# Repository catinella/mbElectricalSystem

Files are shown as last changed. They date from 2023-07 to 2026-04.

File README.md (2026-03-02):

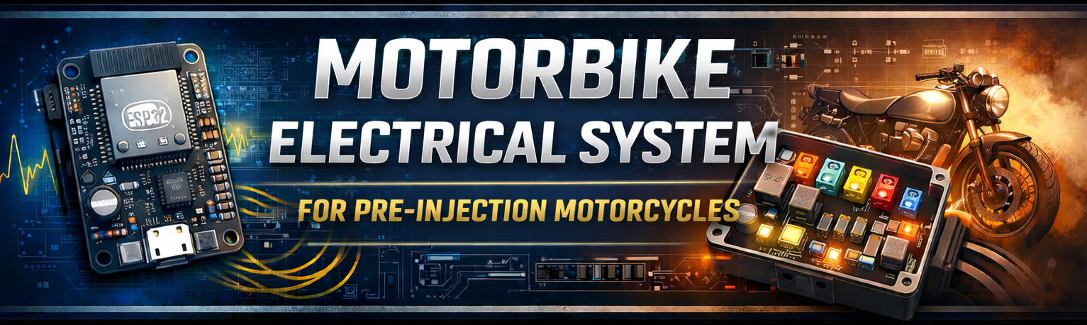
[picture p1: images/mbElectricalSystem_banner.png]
Project's banner

> Modular electrical control unit for pre-injection motorbikes  
> based on ESP32 and distributed power management

## 1.0 Files

| Files/Dirs | Description |
|---|---|
| firmware-esp32 | Firmware for the device's brain |
| images | Images used for README.md file |
| mechanical_parts | The CAD files for the device's box |
| PCB | All the PCB used by the device |

## 2.0 Description:
This project (MBES) aims to realize a generic motorbike electric system you can use on any old motorbike, or customized ones.

Pre-injection motorbikes typically leave the factory with a bulky and highly distributed wiring harness. All power and control
lines are routed through a single large cable bundle, creating what can be described as an “electrical snake”.

Opening this harness often feels like exposing the internal organs of that snake: a dense mass of wires embedded in adhesive
tape and protective compounds. Identifying a single faulty line inside this structure can quickly become a nightmare.

No more chaotic situations with this modern motorbike electrical system: the (bigger) power bales will run just from the device
to the user (light, horn, indicators....) and all commands' cables (light switch, start button, turn indicators switches...)
will be smaller because very small electric current will flow inside them.

### 2.1 Managed devices:
- High beam and down beam headlights
- Left and right turn flashing indicators
- Additional (high power) light
- Horn
- Neutral, left/right indicators, high/down light... LEDs
- STOP light
- Engine start button
- Motorbike (and engine) OFF switch
- Clutch switch
- Decompressor command management
- External cockpit power-connector
- Cockpit's leds

### 2.2 Provided features
- Checking for decompressor command
  The system does not allow the engine to run, before the decompressor command has been activated.
  If the veichle does not have a decompressor system, or if the level control switch is broken, then this feature can be
  disabled easily.

- Direction indicator blinking
  Common blinking for the yellow indicator. The system has been planed for 12V LED indicators (with resistors), but because
  for these ports 2A current can be supported, you can also use older lights

- Resistive authentication key
  In order to turn-on the motorbike, the driver must insert a valid resistor key. After the autentication the key
  can be also removed. It is very usefull for off-road using. 

- Parking mode
  To set the motorbike turned-off but with the normal-light-on and the indicators blinking, you have to put the
  motorbile stopped on its lateral stand, set the engine swith to off, and turn the normal-light on. In this mode the engine
  cannot be started. To restart the veichle you have to turn-off it with the proper switch
	
### 2.3 Security rules:
- Byke stand
  if the motorcycle stand is downn when the engine is connected to the wheels, the the engine will be stopped

- Decompressor command
  If the motorcycle is running and the driver will push the decompressor command, then the engine will be stopped

## 3.0 Info about this version:
This branch is based on ESP32 MCU. This chip is a powerful and very low-price device and it allowed me to reduce the PCB
size. At the moment, I am using the ESP32 devkit device because welder this chip is a bit difficult operation.
This branch solution provides just one PCB. It has further reduced the PCB size.

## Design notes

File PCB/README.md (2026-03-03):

Project's banner

## 1.0 Files

| Files/Directories | Description |
|---|---|
| Connectors.txt | Cables's connectors pin-out |
| create_fabric_files.sh | Script to create the fabric files |
| kicad_symbols | Non standard KiCAD symbols libraries |
| LICENSE.txt | The project's licence file (\*) |
| main.kicad_pcb | The PCB file |
| main.kicad_sch | The main electronic circuit schema |
| mbes_front_outputs.kicad_sch | Power stage circuit |
| mbes_pcbA_connectors.kicad_sch | PCB's connectors electronic circuit  |
| starter_key_plug | The schema of the resistive key |
| images | The images used by this file |

(*) This project is covered by the GPL-3. Please, read that file for further information

## 2.0 Description:
This folder contains all files you need to get and/or modify your own PCB.
To perform these actions you need to install [KiCAD](https://www.kicad.org) software (ver >= 9.0), a free software suite for
electronic design automation (EDA).

## 2.1 Internals:
For the **power stage** I have use the [TPCA8120](https://static.chipdip.ru/lib/624/DOC060624975.pdf) P-Channel MOS. Its
low Drain-source on-resistance (4mOhm) allows me to avoid to waste electric power with high current too. For eample
with a 60W (5A) light it wase just 20mW!! It can also support 10A current and it is very small.

To reduce the number of fuses, the direction indicator LEDs use a [MSMF050](https://www.bourns.com/docs/product-datasheets/mf-msmf.pdf)
PTC Resettable Fuse.

As in all motorbikes, in order to avoid the engine can be started when the motorbike is locked, the proper CDI pin must be
connected to the GND. To achiueve this result and to protect the circuit from unknown electric voltage from the CDI, I have 
used the relay [HK19-DC12V](https://grobotronics.com/images/datasheets/HK19F-12V.pdf) instead of a modern N-Channel MOS.

## 3.0 Devices building:
The following images shows you the PCB shape it should be at the end
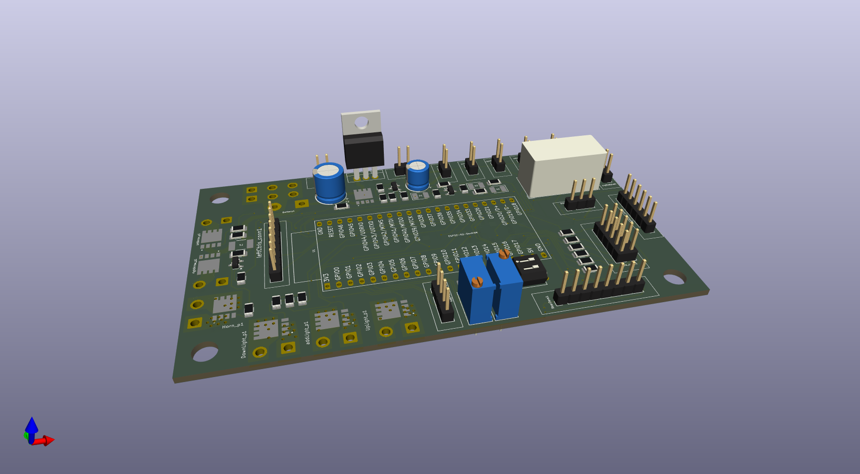
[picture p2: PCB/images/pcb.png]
PCB


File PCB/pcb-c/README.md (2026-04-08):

Project's banner

## 1.0 Files

| Files/Directories | Description |
|---|---|
| pcb-c.kicad_sch | Electric symbolic scheme |
| pcb-c.kicad_pcb | PCB |

(*) This project is covered by the GPL-3. Please, read that file for further information

## 2.0 Description:
This folder contains all files you need to build and/or modify the PCB placed in the rear side of the (DR350) motorbike.
This circuit is a small power stage for the rear light indicators, stop light, and position light. Because all lights
are available in LED format, the power stage is set to provide maximum 500mA (6W) per device.

## 2.1 Internals:
In order to fit this device in the DR350 rear size, I have tried to reduce the required space as much as possible. Also
for this reason, normal fuses have been replaced by [MSMF050](https://www.bourns.com/docs/product-datasheets/mf-msmf.pdf)
PTC Resettable Fuses.

All the power stage's outputs are equivalent but one is dedicated to the motorbike's starter relay. This relay type can
be a big one, often. So, a fly-back diode is very important. For this reason I have used a 
[M7 Rectifiers Diode](https://diotec.com/request/datasheet/m1.pdf).

## 3.0 Devices building:
The following images shows you the PCB shape it should be at the end
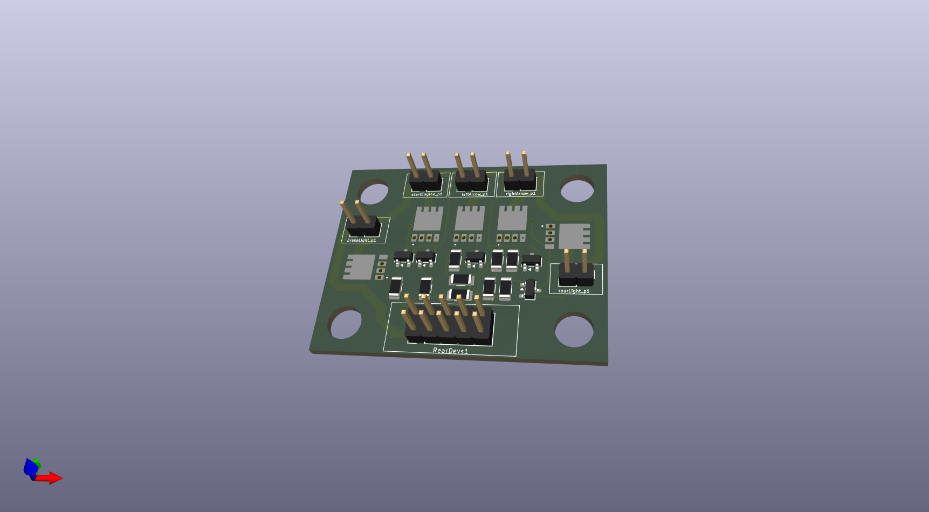
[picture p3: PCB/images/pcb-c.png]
PCB


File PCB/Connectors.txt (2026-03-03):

#-------------------------------------------------------------------------------------------------------------------------------
   __  __       _             _     _ _          _____ _           _        _           _   ____            _                 
  |  \/  | ___ | |_ ___  _ __| |__ (_) | _____  | ____| | ___  ___| |_ _ __(_) ___ __ _| | / ___| _   _ ___| |_ ___ _ __ ___  
  | |\/| |/ _ \| __/ _ \| '__| '_ \| | |/ / _ \ |  _| | |/ _ \/ __| __| '__| |/ __/ _` | | \___ \| | | / __| __/ _ \ '_ ` _ \ 
  | |  | | (_) | || (_) | |  | |_) | |   <  __/ | |___| |  __/ (__| |_| |  | | (_| (_| | |  ___) | |_| \__ \ ||  __/ | | | | |
  |_|  |_|\___/ \__\___/|_|  |_.__/|_|_|\_\___| |_____|_|\___|\___|\__|_|  |_|\___\__,_|_| |____/ \__, |___/\__\___|_| |_| |_|
                                                                                                  |___/                       
#-------------------------------------------------------------------------------------------------------------------------------

Motorbike controls connectors:
	In ordet to connect the handlebars electric (buttons/switches) conrols, I selected connectors based on 2.8mm faston.
	These connectors are widely used in automotive applications, but unfortunately I did not found a link to their
	documentation.

	Left connector pins-map:
	========================             +---+
	1) GND                         +-----+---+-----+
	2) Left turn indicator         | +-+  +-+  +-+ |
	3) Down-light                  | |4|  |5|  |6| |
	4) Dazzling light              | +-+  +-+  +-+ |
	5) Right turn indicator        | +-+  +-+  +-+ |
	6) Horn                        | |1|  |2|  |3| |
	7) Clutch switch               | +-+  +-+  +-+ |
	8) --- N.C. ---                +---------------+

	Right connector pins-map:
	=========================
	1) GND
	2) GND
	3) Brake control switch
	4) Engine START button
	5) Engine OFF
	6) Engine ON

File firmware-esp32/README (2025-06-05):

#----------------------------------------------------------------------------------------------------------------------------------
     __  __       _             _     _ _          _____ _           _        _           _   ____            _                 
    |  \/  | ___ | |_ ___  _ __| |__ (_) | _____  | ____| | ___  ___| |_ _ __(_) ___ __ _| | / ___| _   _ ___| |_ ___ _ __ ___  
    | |\/| |/ _ \| __/ _ \| '__| '_ \| | |/ / _ \ |  _| | |/ _ \/ __| __| '__| |/ __/ _` | | \___ \| | | / __| __/ _ \ '_ ` _ \ 
    | |  | | (_) | || (_) | |  | |_) | |   <  __/ | |___| |  __/ (__| |_| |  | | (_| (_| | |  ___) | |_| \__ \ ||  __/ | | | | |
    |_|  |_|\___/ \__\___/|_|  |_.__/|_|_|\_\___| |_____|_|\___|\___|\__|_|  |_|\___\__,_|_| |____/ \__, |___/\__\___|_| |_| |_|
                                                                                                    |___/                       
#----------------------------------------------------------------------------------------------------------------------------------
0. Files
	build            Folder for firmware building process
	CMakeLists.txt   The CMAKE config file to create the required Makefile
	main             Folder that contains the firmware source code
	sdkconfig        Project and device configuration

1. Description:
	This folder contains all needed files to build the project firmware

	Environment Configuration:
	==========================
	This firmware is based on Espressif's MCU ESP32-S2 and, in order to built it, you have to get and configure the esp-idf
	building environment. To complete the task, please, read the follow official documentation:
		https://docs.espressif.com/projects/esp-idf/en/v5.3.1/esp32/get-started/index.html
	
	Device Configuration:
	=====================
	In order to use the JTAG's pins as normal GPIOs you need to disable the JTAG support on your ESP32-S2 MCU with the
	following command:
		espefuse.py --port /dev/ttyUSB0 burn_efuse SOFT_DIS_JTAG

	Firmware Configuration:
	=======================
	From the 5.3 release esp-idf uses CMAKE as software building infrastructure (project.mk is no more available).
	For this rerason all configuration has been set in the CmakeLists.conf file. This file is parsed by the CmakeLists.txt
	file using the configUtils.cmake library. In order to get the options list, please, read the documentation lines in
	the CmakeLists.txt file's head.

	Building process:
	=================
	To build the firmware use the following idf standard command:
		idf.py build

	Debug console:
	==============
	In order to monitor the pin's status in real-time, you can use the debugConsole software in the <PROJECT HOME>/tool
	folder

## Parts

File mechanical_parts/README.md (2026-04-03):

Project's banner
> Modular electrical control unit for pre-injection motorbikes  
> based on ESP32 and distributed power management

## 1.0 Files

| Files/Dirs | Description |
|---|---|
| DR350_rally | Parts for Suzuki DR350 with rally components |

## 2.0 Description:
This folder contains all CAD and specifications documents dequired to build the Motorbike Electrical System's containers. The
CAD documents are 2D drawings and they show you the flat parts you will have to weller. Anyway, read the README.md file in the
proper sub-folder for further details.

In order to create all the CAD files I used [LibreCAD](https://librecad.org) 2D software. Anyway, because the files are DXF
standard ones, you can use your favourire CAD software.

Any CAD document is composed by (at least) three layers:
- 0        The effective drawing
- builder  Tracks used to build the drawing (you could set it to hidden layer)
- sizes    The measures you need to build the pasts hand made, or to check for their correct shapes

### 2.1 DR350 Rally
The motorbike I used as first model for this project, is a DR350 (1998) modified for off-road using. These changes include a couple
of 48mm Showa front shock absorber and a motorcycle fairing made by [Twalcom](https://www.twalcom.com/en). So the front side box can
be compatible with many similar motorbikes (KTM, Usqvarna...). Instead, the box located in the rear part is just for this motorbyke
model. Infact, the box fills the space originally used for the fuses-box, and the box's shape has been developed to be linked to that
framework in a solid way.

In order to mount this part on your DR350, you need to make 5mm diameter hole in the old metal fuses-box support.

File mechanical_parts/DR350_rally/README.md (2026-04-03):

Project's banner
> Modular electrical control unit for pre-injection motorbikes  
> based on ESP32 and distributed power management

## 1.0 Files

|  Files/Dirs  | Description |
|---|---|
| frontSide | Circuits container for the motorbike front side |
| rearSide | PCB container for the motorbike rear side |

## 2.0 Description:
In the original DR350's electric system, as every other with the same age, the electric current flows in (1mmq) big wires from
the commands to the services (lights, horn, relay...). But the commands are located on the hand-bar, in the front
side of the motorbike, while some services (turn-indicators, stop-light, emgine-start-relay...) is located in the rear one.
So, to reduce the number and the size of the wires that runs in the electric system, I have placed one power stage in the front
side and another in the rear side. Every one of them has its own metal box container.

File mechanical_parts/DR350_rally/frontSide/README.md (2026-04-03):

Project's banner
> Modular electrical control unit for pre-injection motorbikes  
> based on ESP32 and distributed power management

## 1.0 Files

|  Files/Dirs | Description |
|---|---|
| electricSystemBox.dxf | Electric system main-box |
| Koso_instrumentation_attachment.dxf  | Mechanical part used to mount the Koso's cocpit |
| electricSystemBox_squareBars.dxf | System used to close the box's lid |
| motorbikeFrame_attachment_system.dxf | Small plate used to link the box to the framework |

## 2.0 Description:

### 2.1 The Electric System (main) Box
This box can contain the PCB-A and PCB-B circuits. The CAD file shows you all the 2D parts you should create starting from a
3mm aluminium sheet. Mounting the parts to be welled in correct way, can be a difficult task, but you can use the square bars
support to get an advantage.

#### 2.1.1 How to close the box?
In order to close the box's lid, you have to lock the (**electricSystemBox_squareBars.dxf**) square bars inside the box with
3mm screws, then use 5mm screws to lock the lid of the box. For the 3mm screws mounting, I suggest youto use the
[Loctite Threadlocker Red](https://www.loctiteproducts.com/products/central-pdp.html/loctite-threadlocker-red/SAP_0201OHL029W5/variation/209741.html)
substance. You should not need to remove these screws, in the future.

**[IMPORTANT]** Because the bars are used as screw nut, it SHOULD NOT be made with aluminium, it SHOULD be produced using a
stainless steel metal.

#### 2.1.2 How to attach the box to the motorbyke framework?
In order to link the box to the motorbike's framework you should weld four 6MA bolts to the (2mm) plate described in the 
**motorbikeFrame_attachment_system.dxf** drawing. The plate should be placed inside the lid, on the box's bottom side. the
protruding bolts will be used to link the device to the franework in stable way.
The plate and the bolts should be built in stainless steel metal.

### 2.2 Koso's Cokpit
As motorbike cockpit I use a [KOSO's](https://www.koso.com.tw/en) product. To link this part to the upside of the box, you need
two copy of the mechanical single part described in the **Koso_instrumentation_attachment.dxf** CAD file. The file shows you two
sides of the object (from lateral and top point of view). It should be built with aluminium and it does not require to be welded.

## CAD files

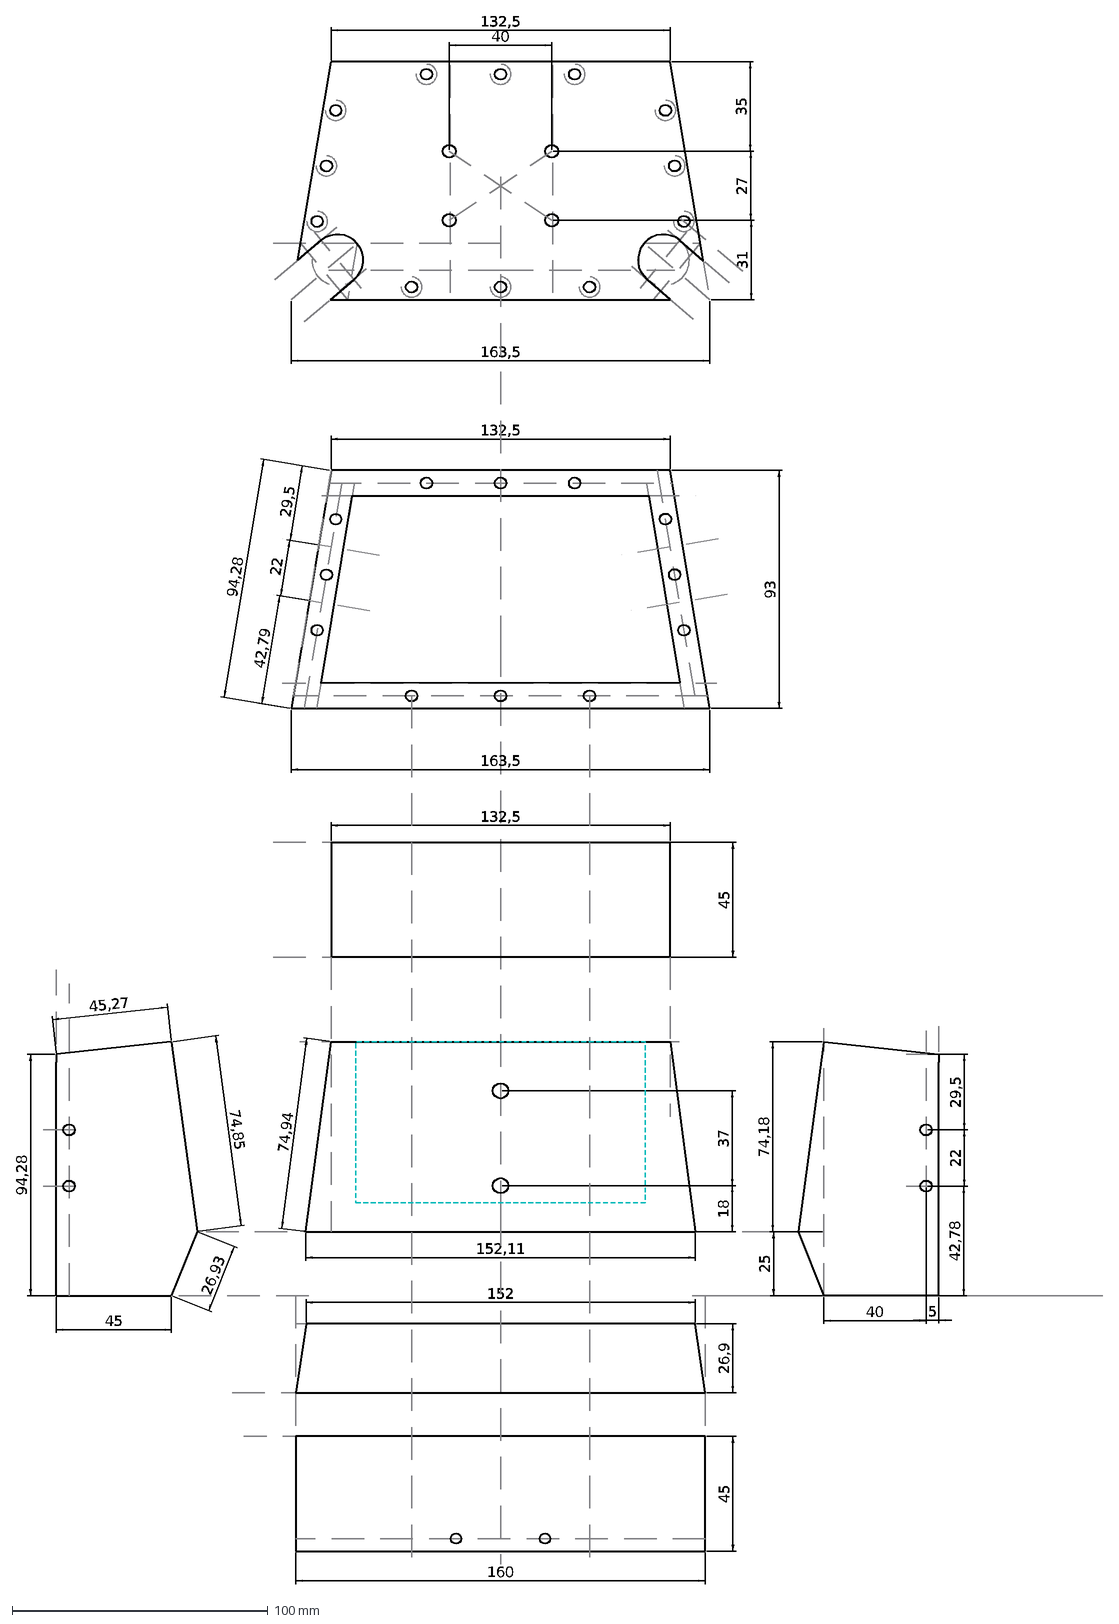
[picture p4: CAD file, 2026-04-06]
mechanical_parts/DR350_rally/frontSide/electricSystemBox.dxf
132,5
163,5
93
45
31
27
35
40
152,11
160
26,9
152
37
18
25
74,18
94,28
26,93
74,85
45,27
74,94
29,5
22
42,79
42,78
5

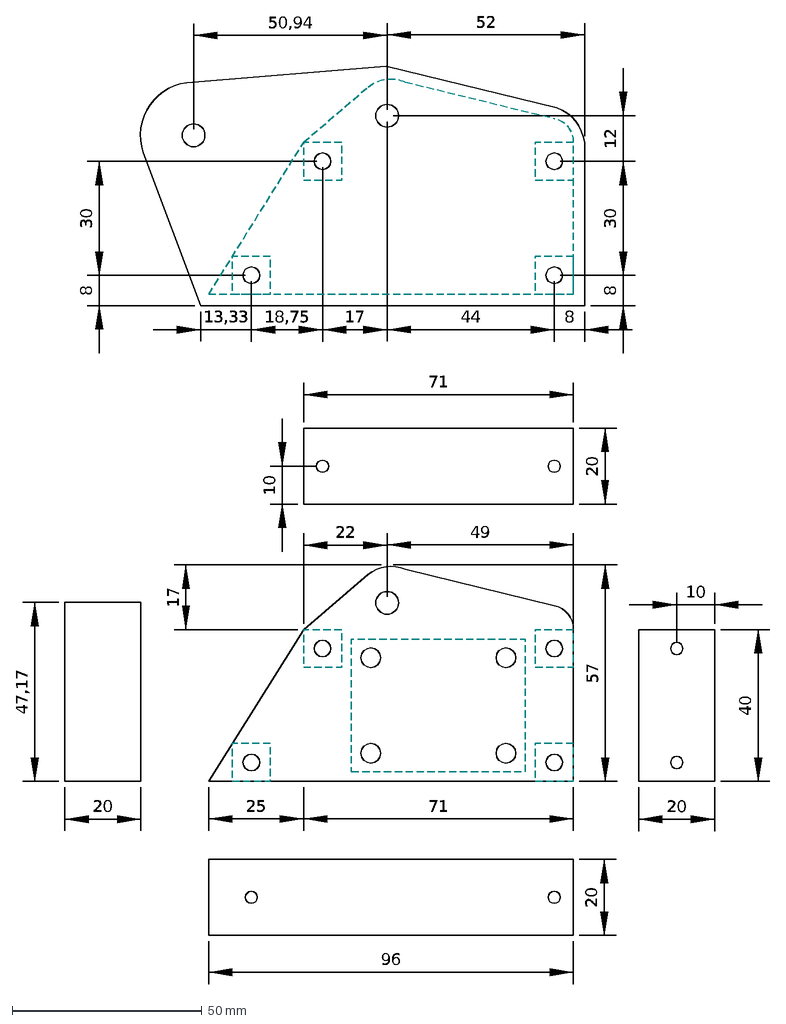
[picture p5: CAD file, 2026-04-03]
mechanical_parts/DR350_rally/rearSide/electricSystemBox.dxf
96
40
57
20
17
49
22
25
71
47,17
10
8
44
30
12
18,75
13,33
52
50,94

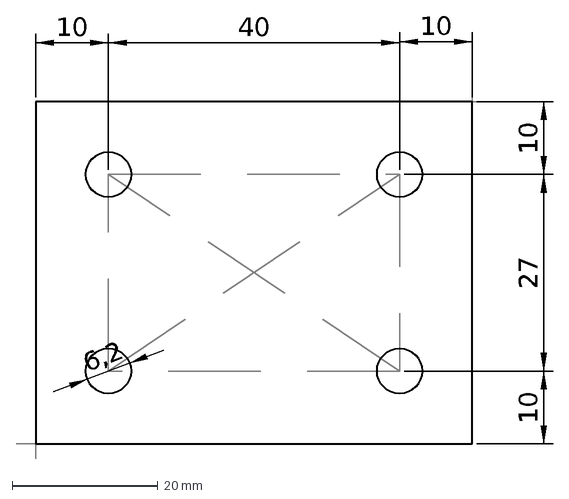
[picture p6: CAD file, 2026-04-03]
mechanical_parts/DR350_rally/frontSide/motorbikeFrame_attachment_system.dxf
10
27
40
6,2

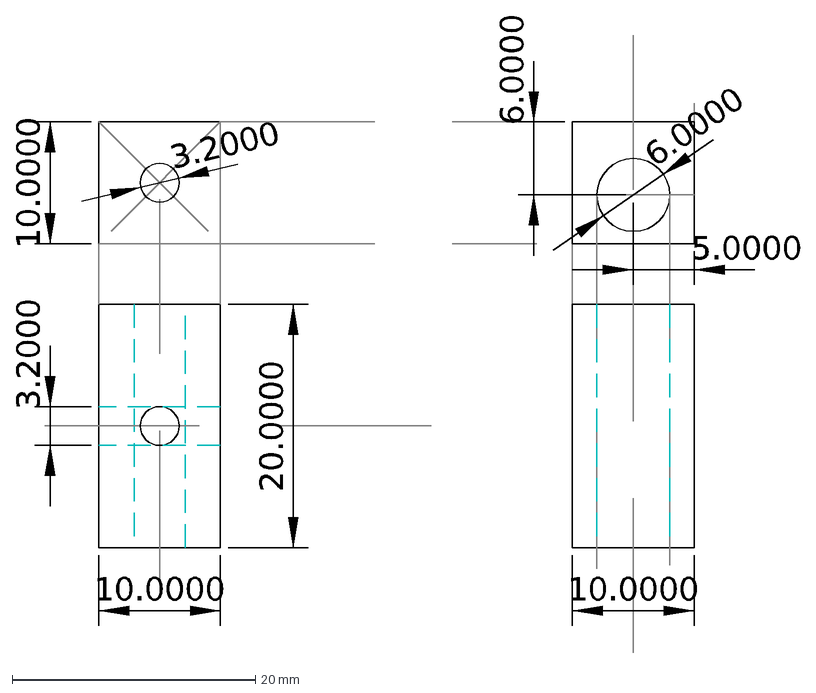
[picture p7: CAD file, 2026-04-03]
mechanical_parts/DR350_rally/rearSide/electricSystemBox_internalSupports.dxf
10.0000
3.2000
20.0000
6.0000
5.0000

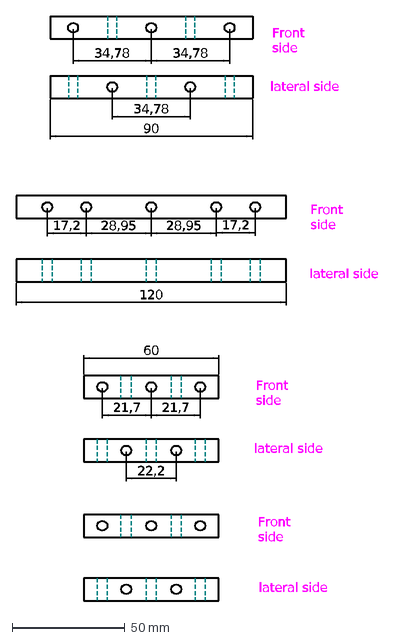
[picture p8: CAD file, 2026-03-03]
mechanical_parts/DR350_rally/frontSide/electricSystemBox_squareBars.dxf
34,78
28,95
17,2
120
60
90
21,7
Front side
lateral side
22,2

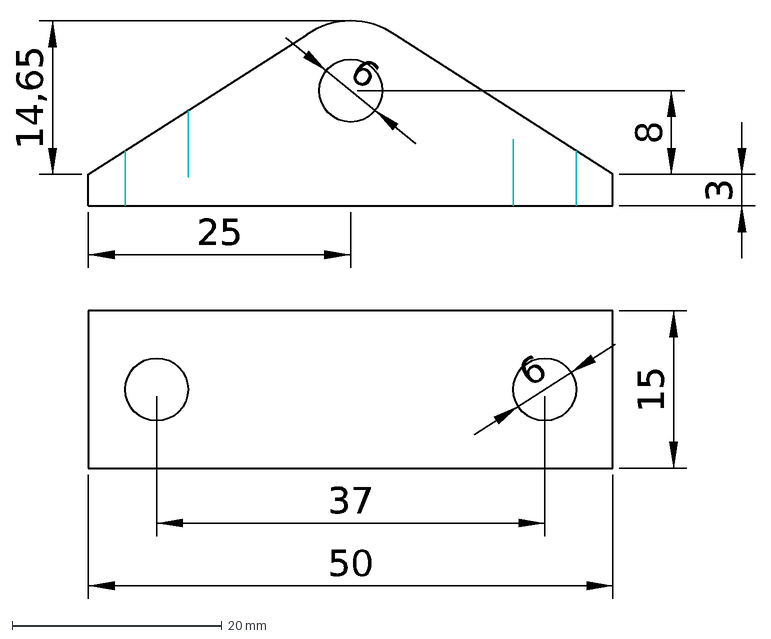
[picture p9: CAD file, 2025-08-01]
mechanical_parts/DR350_rally/frontSide/Koso_instrumentation_attachment.dxf
50
37
25
14,65
8
3
6
15

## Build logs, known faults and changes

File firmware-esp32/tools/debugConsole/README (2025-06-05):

#-----------------------------------------------------------------------------------------------------------------------------------
     __  __       _             _     _ _          _____ _           _        _           _   ____            _                 
    |  \/  | ___ | |_ ___  _ __| |__ (_) | _____  | ____| | ___  ___| |_ _ __(_) ___ __ _| | / ___| _   _ ___| |_ ___ _ __ ___  
    | |\/| |/ _ \| __/ _ \| '__| '_ \| | |/ / _ \ |  _| | |/ _ \/ __| __| '__| |/ __/ _` | | \___ \| | | / __| __/ _ \ '_ ` _ \ 
    | |  | | (_) | || (_) | |  | |_) | |   <  __/ | |___| |  __/ (__| |_| |  | | (_| (_| | |  ___) | |_| \__ \ ||  __/ | | | | |
    |_|  |_|\___/ \__\___/|_|  |_.__/|_|_|\_\___| |_____|_|\___|\___|\__|_|  |_|\___\__,_|_| |____/ \__, |___/\__\___|_| |_| |_|
                                                                                                    |___/                       
#-----------------------------------------------------------------------------------------------------------------------------------
0. Files
	debugConsole.c         C library
	debugConsole.h         Header file
	debugConsole.pl        DebugConsole executable file
	debugConsole_test.pl

1. Description:
	The code belongs to this folder allows you to get a serial debug console where the PINs status will be displayed with the
	log-messages, in ordered and clean way

2. Dependences:
	The process also need the "stty" system-tool to configure the serial port. But this tool should be already installed by
	default

3. Testing procedure
	Because this console receives data from serial port, to test it you need a virtual serial port. In order to get it, you
	can use the following command:
		socat -d -d pty,raw,echo=0 pty,raw,echo=0

	This command will generate a serial ports couple in /dev/pts folder. The two ports are linked like the head and the tail
	of a queue, it means when you send data to a port you can read the data from the other one.

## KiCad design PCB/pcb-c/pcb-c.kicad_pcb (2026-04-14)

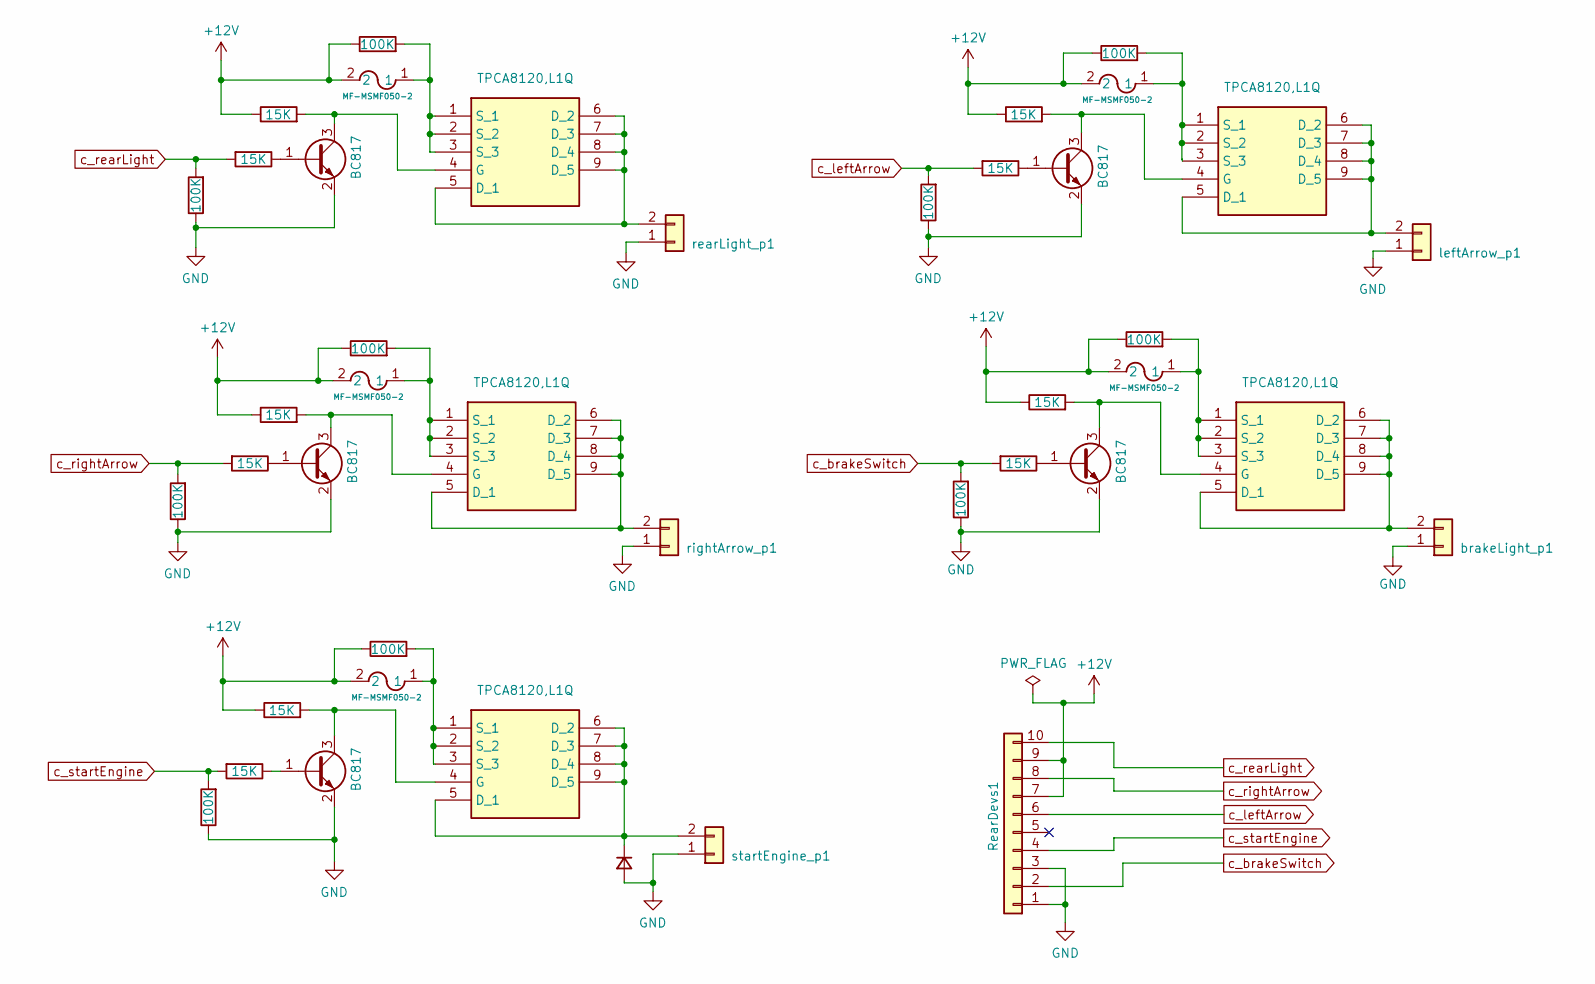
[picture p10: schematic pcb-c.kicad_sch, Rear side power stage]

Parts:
D1: M7; D_2114_3652Metric_Pad1.85x3.75mm_HandSolder
F1, F2, F3, F4, F5: MF-MSMF050-2; FUSE_F050-2
Q1, Q3, Q4, Q6, Q8: BC817; SOT-23
Q2, Q5, Q7, Q9, Q13: TPCA8120,L1Q; TPH4R003NLL1Q; Manufacturer_Part_Number TPCA8120,L1Q; Mouser Part Number 757-TPCA8120L1Q
R1, R3, R6, R8, R11, R12, R15, R16, R19, R21: 100K; R_1206_3216Metric
R2, R4, R5, R7, R9, R10, R13, R14, R17, R18: 15K; R_1206_3216Metric
RearDevs1: Conn_01x10; PinHeader_2x05_P2.54mm_Vertical
brakeLight_p1: Conn_01x02; PinHeader_1x02_P2.54mm_Vertical
leftArrow_p1: Conn_01x02; PinHeader_1x02_P2.54mm_Vertical
rearLight_p1: Conn_01x02; PinHeader_1x02_P2.54mm_Vertical
rightArrow_p1: Conn_01x02; PinHeader_1x02_P2.54mm_Vertical
startEngine_p1: Conn_01x02; PinHeader_1x02_P2.54mm_Vertical

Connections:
+12V: F1.2, F2.2, F3.2, F4.2, F5.2, R2.1, R3.1, R5.1, R6.1, R10.1, R11.1, R14.1, R15.1, R18.1, R19.1, RearDevs1.7, RearDevs1.9
GND: D1.2 (A), Q1.2 (E), Q3.2 (E), Q4.2 (E), Q6.2 (E), Q8.2 (E), R1.1, R8.1, R12.1, R16.1, R21.1, RearDevs1.1, RearDevs1.3, brakeLight_p1.1, leftArrow_p1.1, rearLight_p1.1, rightArrow_p1.1, startEngine_p1.1
unnamed: D1.1 (K), Q5.5 (D_1), Q5.6 (D_2), Q5.7 (D_3), Q5.8 (D_4), Q5.9 (D_5), startEngine_p1.2
unnamed: Q1.1 (B), R4.1
unnamed: Q1.3 (C), Q2.4 (G), R5.2
unnamed: Q2.5 (D_1), Q2.6 (D_2), Q2.7 (D_3), Q2.8 (D_4), Q2.9 (D_5), brakeLight_p1.2
unnamed: F2.1, Q2.1 (S_1), Q2.2 (S_2), Q2.3 (S_3), R6.2
unnamed: Q3.1 (B), R7.1
unnamed: Q4.1 (B), R9.1
unnamed: Q4.3 (C), Q5.4 (G), R10.2
unnamed: F5.1, Q5.1 (S_1), Q5.2 (S_2), Q5.3 (S_3), R3.2
unnamed: Q6.1 (B), R13.1
unnamed: Q6.3 (C), Q7.4 (G), R14.2
unnamed: Q7.5 (D_1), Q7.6 (D_2), Q7.7 (D_3), Q7.8 (D_4), Q7.9 (D_5), leftArrow_p1.2
unnamed: F4.1, Q7.1 (S_1), Q7.2 (S_2), Q7.3 (S_3), R15.2
unnamed: Q8.1 (B), R17.1
unnamed: Q8.3 (C), Q9.4 (G), R18.2
unnamed: Q9.5 (D_1), Q9.6 (D_2), Q9.7 (D_3), Q9.8 (D_4), Q9.9 (D_5), rightArrow_p1.2
unnamed: F1.1, Q9.1 (S_1), Q9.2 (S_2), Q9.3 (S_3), R11.2
unnamed: Q13.5 (D_1), Q13.6 (D_2), Q13.7 (D_3), Q13.8 (D_4), Q13.9 (D_5), rearLight_p1.2
unnamed: Q3.3 (C), Q13.4 (G), R2.2
unnamed: F3.1, Q13.1 (S_1), Q13.2 (S_2), Q13.3 (S_3), R19.2
c_brakeSwitch: R1.2, R4.2, RearDevs1.2
c_leftArrow: R12.2, R13.2, RearDevs1.6
c_rearLight: R7.2, R21.2, RearDevs1.10
c_rightArrow: R16.2, R17.2, RearDevs1.8
c_startEngine: R8.2, R9.2, RearDevs1.4

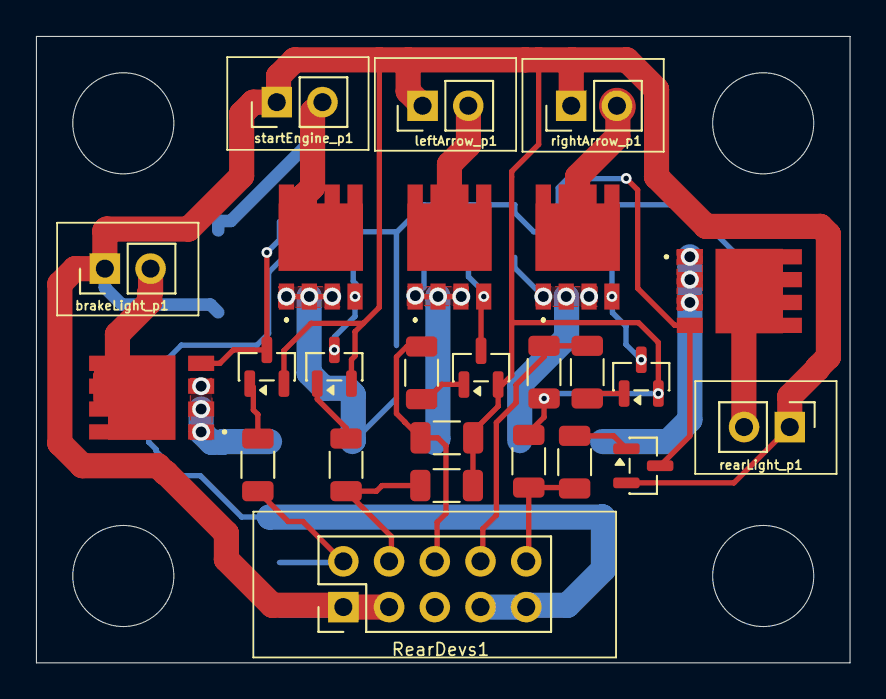
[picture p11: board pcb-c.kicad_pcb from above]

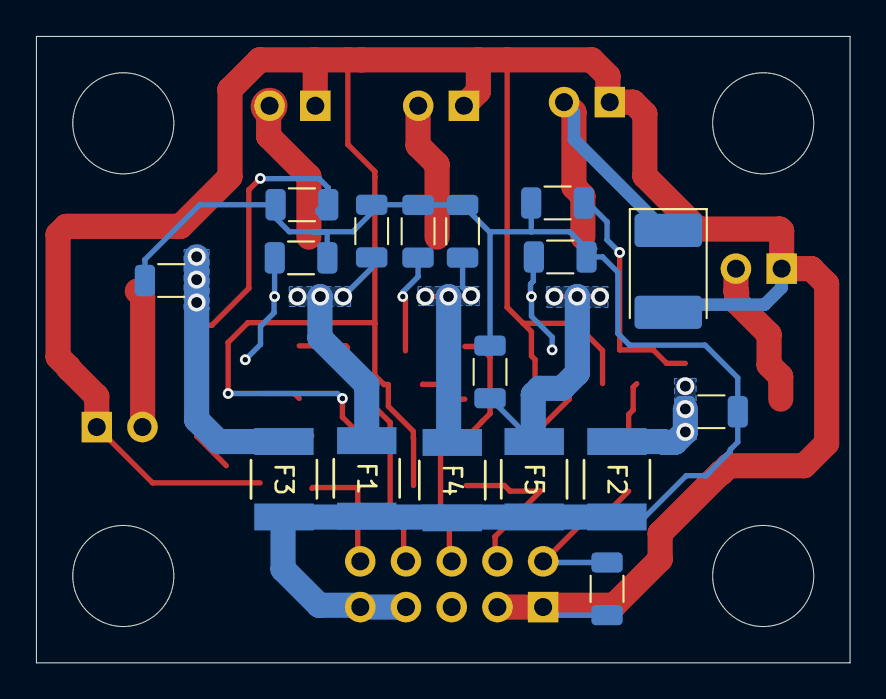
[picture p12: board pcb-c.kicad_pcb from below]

Board: 2 copper layers, 45.2 x 34.8 mm, 42 parts (17 on the bottom side), 27 nets.

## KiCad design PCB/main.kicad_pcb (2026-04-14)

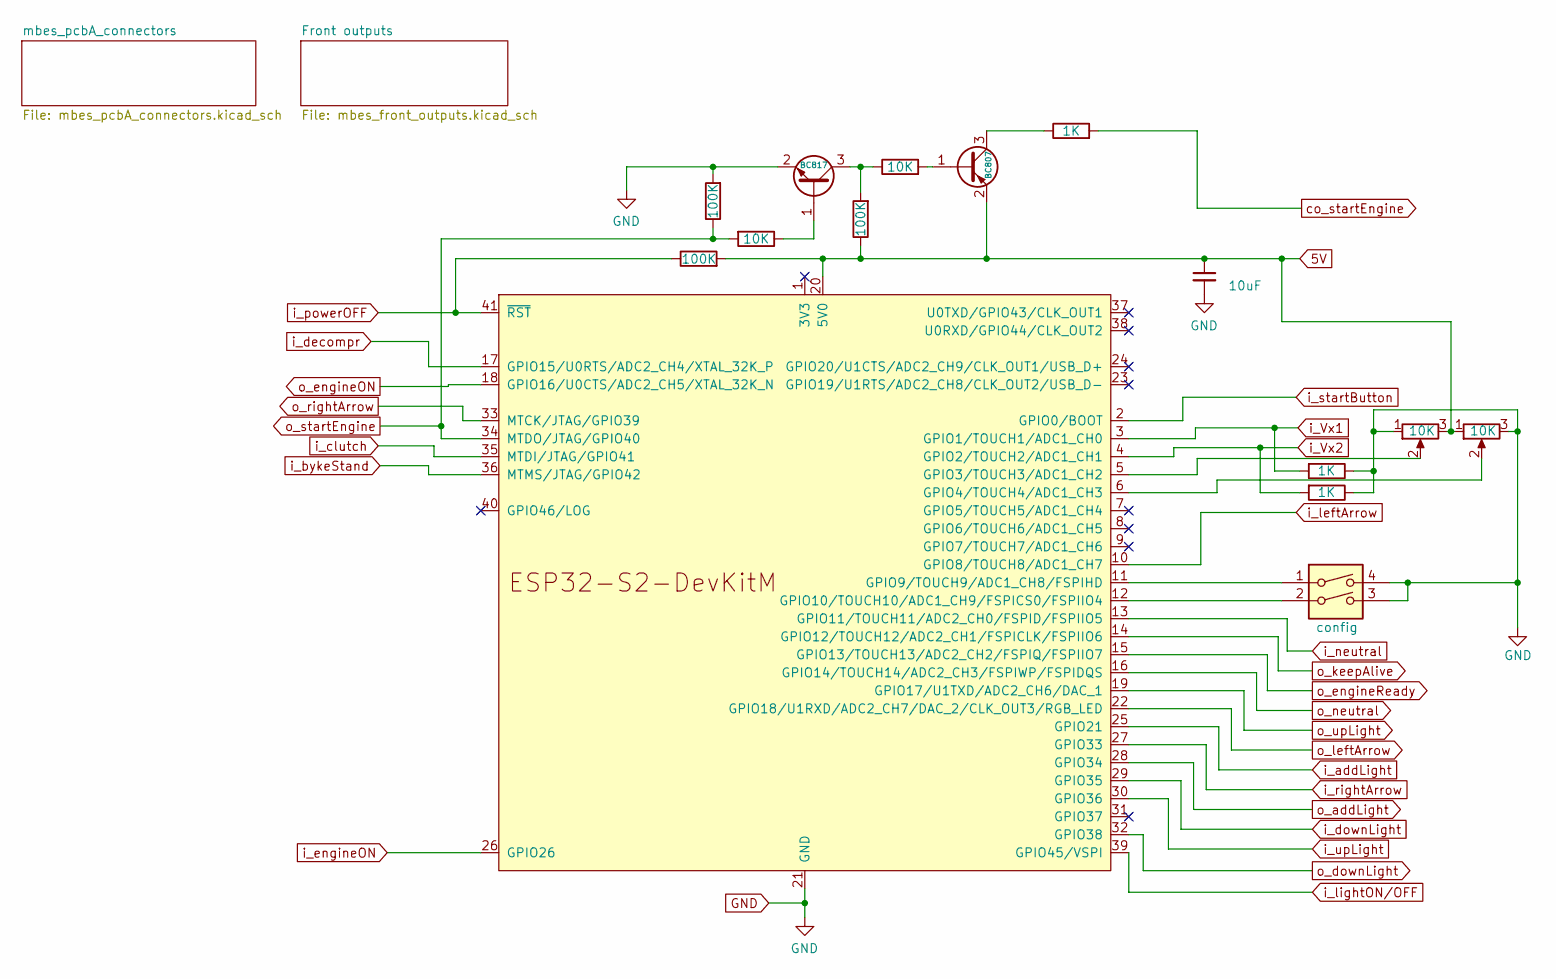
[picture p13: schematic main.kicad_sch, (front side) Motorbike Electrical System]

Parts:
C1: 10uF; CP_Radial_D6.3mm_P2.50mm
Q19: BC817; SOT-23
Q23: BC807; SOT-23
R1, R5, R14: 100K; R_1206_3216Metric
R2: 10K; R_1206_3216Metric
R3, R4: 1K; R_1206_3216Metric
RA49: 10K; R_1206_3216Metric
RA51: 1K; R_1206_3216Metric
RV1, RV2: 10K; Potentiometer_Bourns_3296W_Vertical
SW1: config; SW_DIP_SPSTx02_Slide_6.7x6.64mm_W7.62mm_P2.54mm_LowProfile
U1: ESP32-S2-DevKitM

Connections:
5V: C1.1, Q23.2 (E), R1.2, R5.1, RV1.3, RV2.1, U1.20 (5V0); also elsewhere on the board
GND: C1.2, Q19.2 (E), R3.1, R4.1, R14.2, RV1.1, RV2.3, SW1.3, SW1.4, U1.21 (GND), U1.42 (GND); also elsewhere on the board
unnamed: Q19.1 (B), R2.1
unnamed: Q19.3 (C), R5.2, RA49.1
unnamed: Q23.1 (B), RA49.2
unnamed: Q23.3 (C), RA51.1
unnamed: RV1.2, U1.5 (GPIO3/TOUCH3/ADC1_CH2)
unnamed: RV2.2, U1.6 (GPIO4/TOUCH4/ADC1_CH3)
unnamed: SW1.1, U1.11 (GPIO9/TOUCH9/ADC1_CH8/FSPIHD)
unnamed: SW1.2, U1.12 (GPIO10/TOUCH10/ADC1_CH9/FSPICS0/FSPIIO4)
co_startEngine: RA51.2; also elsewhere on the board
i_Vx1: R3.2, U1.3 (GPIO1/TOUCH1/ADC1_CH0); also elsewhere on the board
i_Vx2: R4.2, U1.4 (GPIO2/TOUCH2/ADC1_CH1); also elsewhere on the board
i_addLight: U1.25 (GPIO21); also elsewhere on the board
i_bykeStand: U1.36 (MTMS/JTAG/GPIO42); also elsewhere on the board
i_clutch: U1.35 (MTDI/JTAG/GPIO41); also elsewhere on the board
i_decompr: U1.17 (GPIO15/U0RTS/ADC2_CH4/XTAL_32K_P); also elsewhere on the board
i_downLight: U1.29 (GPIO35); also elsewhere on the board
i_engineON: U1.26 (GPIO26); also elsewhere on the board
i_leftArrow: U1.10 (GPIO8/TOUCH8/ADC1_CH7); also elsewhere on the board
i_lightON/OFF: U1.39 (GPIO45/VSPI); also elsewhere on the board
i_neutral: U1.13 (GPIO11/TOUCH11/ADC2_CH0/FSPID/FSPIIO5); also elsewhere on the board
i_powerOFF: R1.1, U1.41 (~RST); also elsewhere on the board
i_rightArrow: U1.27 (GPIO33); also elsewhere on the board
i_startButton: U1.2 (GPIO0/BOOT); also elsewhere on the board
i_upLight: U1.30 (GPIO36); also elsewhere on the board
o_addLight: U1.28 (GPIO34); also elsewhere on the board
o_downLight: U1.32 (GPIO38); also elsewhere on the board
o_engineON: U1.18 (GPIO16/U0CTS/ADC2_CH5/XTAL_32K_N); also elsewhere on the board
o_engineReady: U1.15 (GPIO13/TOUCH13/ADC2_CH2/FSPIQ/FSPIIO7); also elsewhere on the board
o_keepAlive: U1.14 (GPIO12/TOUCH12/ADC2_CH1/FSPICLK/FSPIIO6); also elsewhere on the board
o_leftArrow: U1.22 (GPIO18/U1RXD/ADC2_CH7/DAC_2/CLK_OUT3/RG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); also elsewhere on the board
o_neutral: U1.16 (GPIO14/TOUCH14/ADC2_CH3/FSPIWP/FSPIDQS); also elsewhere on the board
o_rightArrow: U1.33 (MTCK/JTAG/GPIO39); also elsewhere on the board
o_startEngine: R2.2, R14.1, U1.34 (MTDO/JTAG/GPIO40)
o_upLight: U1.19 (GPIO17/U1TXD/ADC2_CH6/DAC_1); also elsewhere on the board

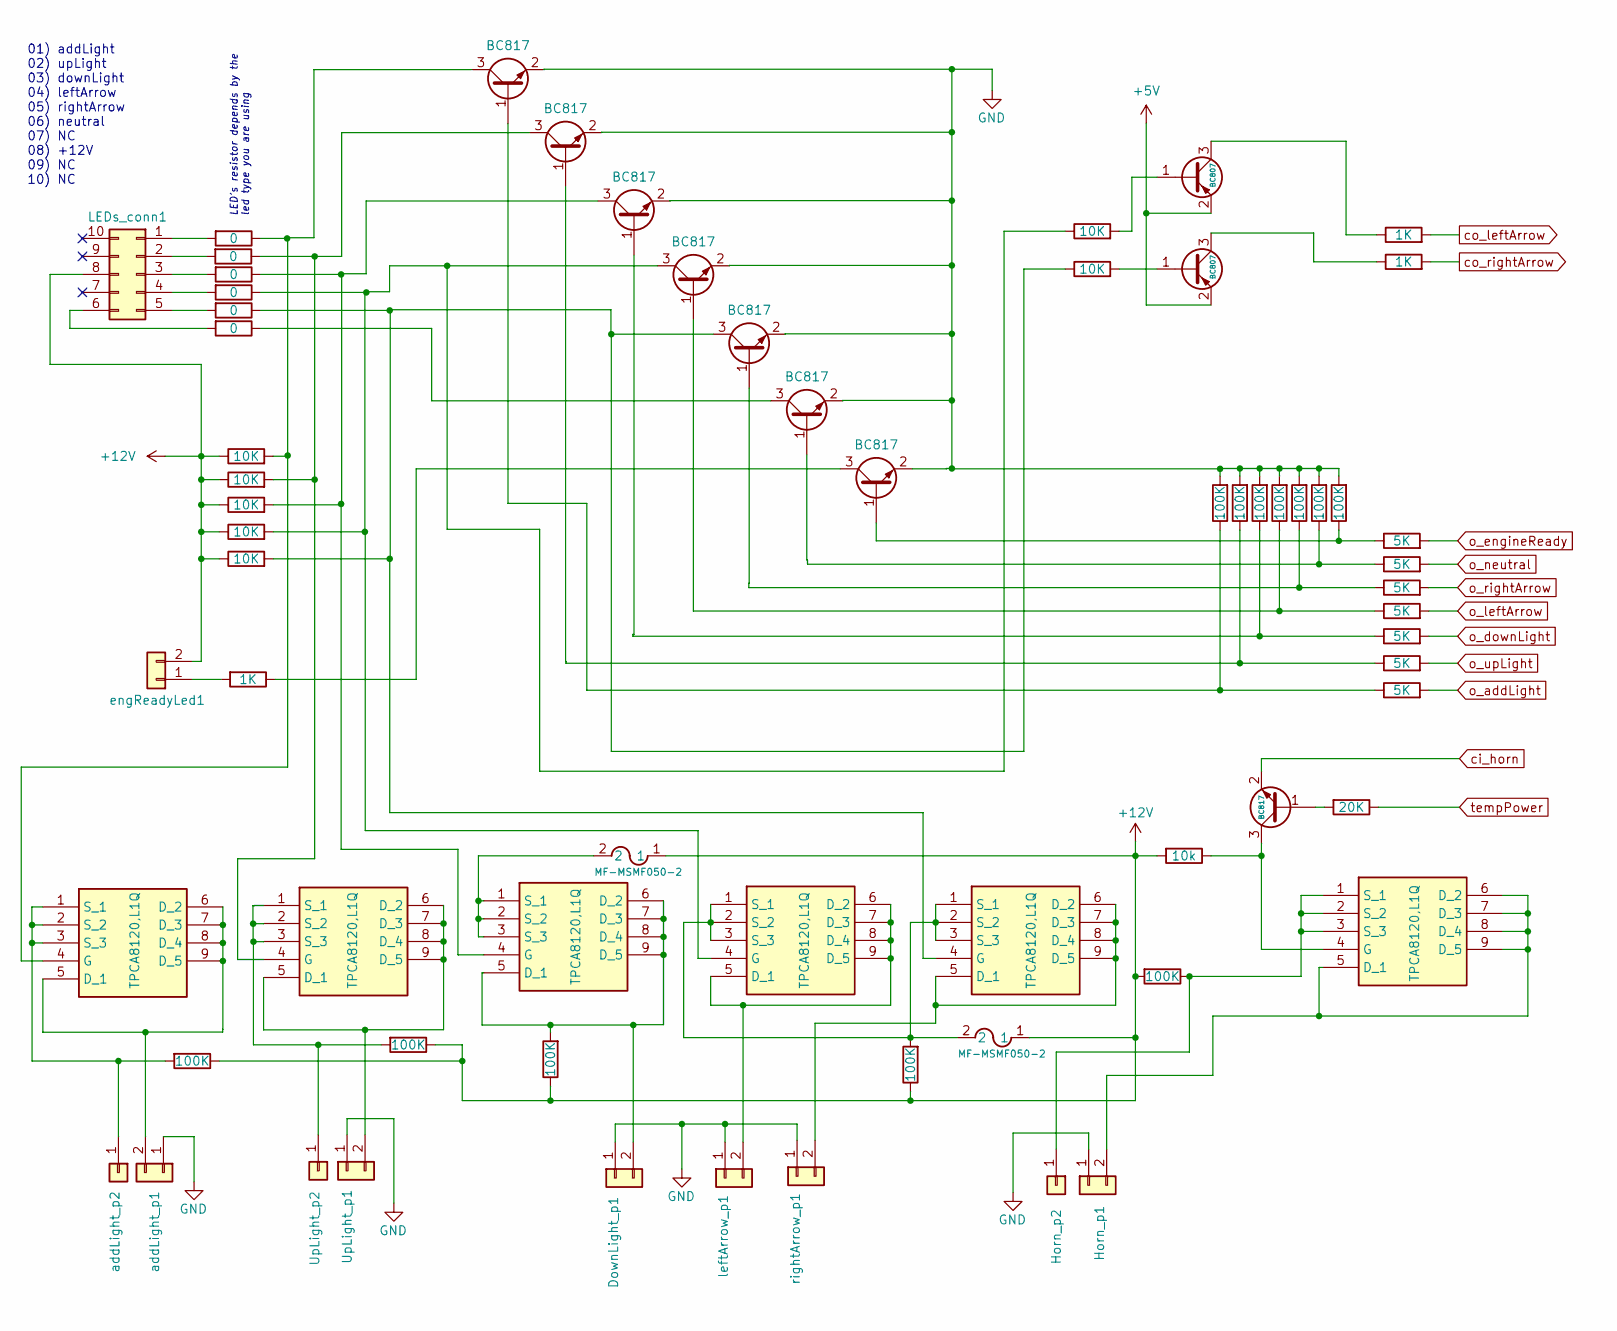
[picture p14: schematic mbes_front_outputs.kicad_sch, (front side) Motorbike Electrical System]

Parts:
DownLight_p1: Conn_01x02; PinHeader_1x02_P2.54mm_Vertical
F1, F2: MF-MSMF050-2; FUSE_F050-2
Horn_p1: Conn_01x02; JST_VH_B2P-VH-FB-B_1x02_P3.96mm_Vertical
Horn_p2: Conn_01x01; SolderWire-1sqmm_1x01_D1.4mm_OD2.7mm
LEDs_conn1: Conn_02x05_Counter_Clockwise; PinHeader_2x05_P2.54mm_Vertical
Q1, Q20: BC807; SOT-23
Q5, Q6, Q7, Q12, Q16, Q18: TPCA8120,L1Q; TPH4R003NLL1Q; Mouser Part Number 757-TPCA8120L1Q
Q8, Q9, Q10, Q11, Q13, Q14, Q15, Q17: BC817; SOT-23
RA3, RA4, RA5, RA6, RA7, RA8: 0; R_1206_3216Metric
RA9, RA10, RA11, RA12, RA13, RA37, RA38: 10K; R_1206_3216Metric
RA14, RA43, RA44: 1K; R_1206_3216Metric
RA15, RA16, RA17, RA18, RA19, RA20, RA22, RA23, RA24, RA25, RA27, RA28: 100K; R_1206_3216Metric
RA21: 10k; R_1206_3216Metric
RA29: 20K; R_1206_3216Metric
RA30, RA31, RA32, RA33, RA34, RA35, RA36: 5K; R_1206_3216Metric
UpLight_p1: Conn_01x02; JST_VH_B2P-VH-FB-B_1x02_P3.96mm_Vertical
UpLight_p2: Conn_01x01; SolderWire-1sqmm_1x01_D1.4mm_OD2.7mm
addLight_p1: Conn_01x02; JST_VH_B2P-VH-FB-B_1x02_P3.96mm_Vertical
addLight_p2: Conn_01x01; SolderWire-1sqmm_1x01_D1.4mm_OD2.7mm
engReadyLed1: Conn_01x02; PinHeader_1x02_P2.54mm_Vertical
leftArrow_p1: Conn_01x02; PinHeader_1x02_P2.54mm_Vertical
rightArrow_p1: Conn_01x02; PinHeader_1x02_P2.54mm_Vertical

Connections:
5V: Q1.2 (E), Q20.2 (E); also elsewhere on the board
+12V: F1.1, F2.1, LEDs_conn1.8, RA9.1, RA10.1, RA11.1, RA12.1, RA13.1, RA15.1, RA16.1, RA17.1, RA18.1, RA19.2, RA21.2, engReadyLed1.2; also elsewhere on the board
GND: DownLight_p1.1, Horn_p1.1, Q8.2 (E), Q9.2 (E), Q10.2 (E), Q11.2 (E), Q13.2 (E), Q14.2 (E), Q15.2 (E), RA20.2, RA22.2, RA23.2, RA24.2, RA25.2, RA27.2, RA28.2, UpLight_p1.1, addLight_p1.1, leftArrow_p1.1, rightArrow_p1.1; also elsewhere on the board
unnamed: DownLight_p1.2, Q7.5 (D_1), Q7.6 (D_2), Q7.7 (D_3), Q7.8 (D_4), Q7.9 (D_5), RA17.2
unnamed: Horn_p1.2, Q18.5 (D_1), Q18.6 (D_2), Q18.7 (D_3), Q18.8 (D_4), Q18.9 (D_5)
unnamed: Horn_p2.1, Q18.1 (S_1), Q18.2 (S_2), Q18.3 (S_3), RA19.1
unnamed: LEDs_conn1.1, RA4.2
unnamed: LEDs_conn1.2, RA3.2
unnamed: LEDs_conn1.3, RA5.2
unnamed: LEDs_conn1.4, RA6.2
unnamed: LEDs_conn1.5, RA7.2
unnamed: LEDs_conn1.6, RA8.2
unnamed: Q1.1 (B), RA37.2
unnamed: Q1.3 (C), RA43.1
unnamed: Q5.5 (D_1), Q5.6 (D_2), Q5.7 (D_3), Q5.8 (D_4), Q5.9 (D_5), addLight_p1.2
unnamed: Q5.4 (G), Q8.3 (C), RA4.1, RA9.2
unnamed: Q5.1 (S_1), Q5.2 (S_2), Q5.3 (S_3), RA15.2, addLight_p2.1
unnamed: Q6.5 (D_1), Q6.6 (D_2), Q6.7 (D_3), Q6.8 (D_4), Q6.9 (D_5), UpLight_p1.2
unnamed: Q6.4 (G), Q9.3 (C), RA3.1, RA10.2
unnamed: Q6.1 (S_1), Q6.2 (S_2), Q6.3 (S_3), RA16.2, UpLight_p2.1
unnamed: F2.2, Q7.1 (S_1), Q7.2 (S_2), Q7.3 (S_3)
unnamed: Q8.1 (B), RA20.1, RA36.1
unnamed: Q9.1 (B), RA22.1, RA35.1
unnamed: Q10.1 (B), RA23.1, RA34.1
unnamed: Q7.4 (G), Q10.3 (C), RA5.1, RA11.2
unnamed: Q11.1 (B), RA24.1, RA33.1
unnamed: Q11.3 (C), Q12.4 (G), RA6.1, RA12.2, RA37.1
unnamed: Q12.5 (D_1), Q12.6 (D_2), Q12.7 (D_3), Q12.8 (D_4), Q12.9 (D_5), leftArrow_p1.2
unnamed: F1.2, Q12.1 (S_1), Q12.2 (S_2), Q12.3 (S_3), Q16.1 (S_1), Q16.2 (S_2), Q16.3 (S_3), RA18.2
unnamed: Q13.1 (B), RA25.1, RA32.1
unnamed: Q13.3 (C), Q16.4 (G), RA7.1, RA13.2, RA38.1
unnamed: Q14.1 (B), RA27.1, RA31.1
unnamed: Q14.3 (C), RA8.1
unnamed: Q15.1 (B), RA28.1, RA30.1
unnamed: Q15.3 (C), RA14.1
unnamed: Q16.5 (D_1), Q16.6 (D_2), Q16.7 (D_3), Q16.8 (D_4), Q16.9 (D_5), rightArrow_p1.2
unnamed: Q17.1 (B), RA29.2
unnamed: Q17.3 (C), Q18.4 (G), RA21.1
unnamed: Q20.1 (B), RA38.2
unnamed: Q20.3 (C), RA44.1
unnamed: RA14.2, engReadyLed1.1
ci_horn: Q17.2 (E); also elsewhere on the board
co_leftArrow: RA43.2; also elsewhere on the board
co_rightArrow: RA44.2; also elsewhere on the board
o_addLight: RA36.2; also elsewhere on the board
o_downLight: RA34.2; also elsewhere on the board
o_engineReady: RA30.2; also elsewhere on the board
o_leftArrow: RA33.2; also elsewhere on the board
o_neutral: RA31.2; also elsewhere on the board
o_rightArrow: RA32.2; also elsewhere on the board
o_upLight: RA35.2; also elsewhere on the board
tempPower: RA29.1; also elsewhere on the board

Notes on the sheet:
LED's resistor depends by the led type you are using
01) addLight 02) upLight 03) downLight 04) leftArrow 05) rightArrow 06) neutral 07) NC 08) +12V 09) NC 10) NC

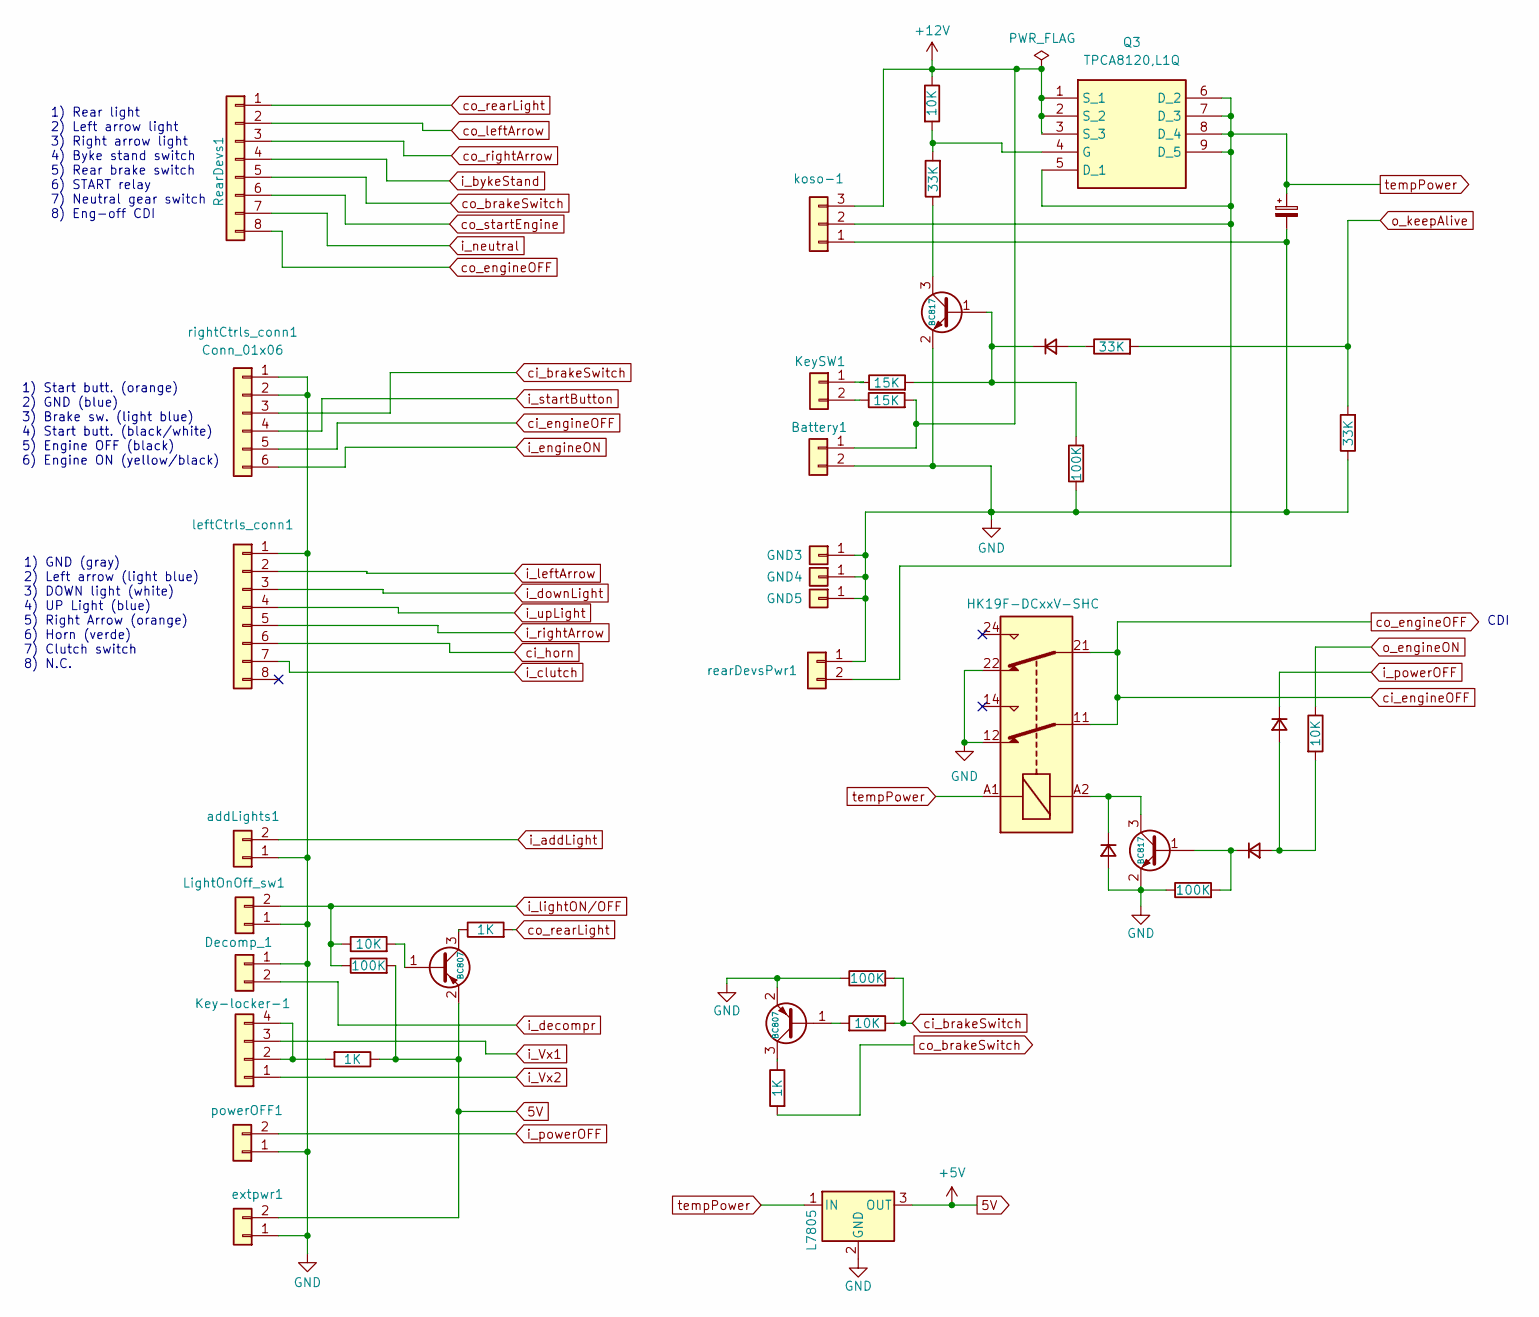
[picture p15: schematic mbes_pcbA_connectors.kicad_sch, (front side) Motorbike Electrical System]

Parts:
Battery1: Conn_01x02; JST_VH_B2P-VH-FB-B_1x02_P3.96mm_Vertical
C2: C_Polarized_Small; CP_Radial_D8.0mm_P2.50mm
D1, D2, D3: PMEG40T30ER; Nexperia_CFP3_SOD-123W
Decomp_1: Conn_01x02; PinHeader_1x02_P2.54mm_Vertical
GND3, GND4, GND5: Conn_01x01; SolderWire-1sqmm_1x01_D1.4mm_OD2.7mm
K1: HK19F-DCxxV-SHC; Relay_DPDT_Finder_30.22
Key-locker-1: Conn_01x04; PinHeader_1x04_P2.54mm_Vertical
KeySW1: Conn_01x02; PinHeader_1x02_P2.54mm_Vertical
LightOnOff_sw1: Conn_01x02; PinHeader_1x02_P2.54mm_Vertical
Q2, Q4: BC817; SOT-23
Q3: TPCA8120,L1Q; TPH4R003NLL1Q; Manufacturer_Part_Number TPCA8120,L1Q; Mouser Part Number 757-TPCA8120L1Q
Q22, Q24: BC807; SOT-23
R6: 1K; R_1206_3216Metric
R7, R8: 15K; R_1206_3216Metric
R9: 10K; R_1206_3216Metric
R10, R11, R12: 33K; R_1206_3216Metric
R13: 100K; R_1206_3216Metric
RA1, RA41, RA47: 100K; R_1206_3216Metric
RA2, RA40, RA46: 10K; R_1206_3216Metric
RA42, RA48: 1K; R_1206_3216Metric
RearDevs1: Conn_01x08; PinHeader_1x08_P2.54mm_Vertical
U2: L7805; TO-220-3_Vertical
addLights1: Conn_01x02; PinHeader_1x02_P2.54mm_Vertical
extpwr1: Conn_01x02; PinHeader_1x02_P2.54mm_Vertical
flyback-1: PMEG40T30ER; Nexperia_CFP3_SOD-123W
koso-1: Conn_01x03; PinHeader_1x03_P2.54mm_Vertical
leftCtrls_conn1: Conn_01x08; PinHeader_1x08_P2.54mm_Vertical
powerOFF1: Conn_01x02; PinHeader_1x02_P2.54mm_Vertical
rearDevsPwr1: Conn_01x02; PinHeader_1x02_P2.54mm_Vertical
rightCtrls_conn1: Conn_01x06; PinHeader_1x06_P2.54mm_Vertical

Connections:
5V: Q22.2 (E), R6.1, RA47.2, U2.3 (OUT), extpwr1.2; also elsewhere on the board
+12V: Battery1.1, Q3.1 (S_1), Q3.2 (S_2), Q3.3 (S_3), R7.2, R9.1, koso-1.3; also elsewhere on the board
GND: Battery1.2, C2.2, Decomp_1.1, GND3.1, GND4.1, GND5.1, K1.12, K1.22, LightOnOff_sw1.1, Q2.2 (E), Q4.2 (E), Q24.2 (E), R12.1, R13.1, RA1.1, RA41.1, U2.2 (GND), addLights1.1, extpwr1.1, flyback-1.2 (A), koso-1.1, leftCtrls_conn1.1, powerOFF1.1, rearDevsPwr1.1, rightCtrls_conn1.1, rightCtrls_conn1.2; also elsewhere on the board
unnamed: D1.2 (A), R11.1
unnamed: D1.1 (K), Q2.1 (B), R8.2, R13.2
unnamed: D2.2 (A), D3.2 (A), RA2.2
unnamed: D2.1 (K), Q4.1 (B), RA1.2
unnamed: Key-locker-1.2, Key-locker-1.4, R6.2
unnamed: KeySW1.1, R8.1
unnamed: KeySW1.2, R7.1
unnamed: Q2.3 (C), R10.1
unnamed: Q3.4 (G), R9.2, R10.2
unnamed: K1.A2, Q4.3 (C), flyback-1.1 (K)
unnamed: Q22.1 (B), RA46.2
unnamed: Q22.3 (C), RA48.1
unnamed: Q24.1 (B), RA40.2
unnamed: Q24.3 (C), RA42.1
ci_brakeSwitch: RA40.1, RA41.2, rightCtrls_conn1.3
ci_engineOFF: K1.11, K1.21, RearDevs1.8, rightCtrls_conn1.5
ci_horn: leftCtrls_conn1.6; also elsewhere on the board
co_brakeSwitch: RA42.2, RearDevs1.5
co_leftArrow: RearDevs1.2; also elsewhere on the board
co_rearLight: RA48.2, RearDevs1.1
co_rightArrow: RearDevs1.3; also elsewhere on the board
co_startEngine: RearDevs1.6; also elsewhere on the board
i_Vx1: Key-locker-1.3; also elsewhere on the board
i_Vx2: Key-locker-1.1; also elsewhere on the board
i_addLight: addLights1.2; also elsewhere on the board
i_bykeStand: RearDevs1.4; also elsewhere on the board
i_clutch: leftCtrls_conn1.7; also elsewhere on the board
i_decompr: Decomp_1.2; also elsewhere on the board
i_downLight: leftCtrls_conn1.3; also elsewhere on the board
i_engineON: rightCtrls_conn1.6; also elsewhere on the board
i_leftArrow: leftCtrls_conn1.2; also elsewhere on the board
i_lightON/OFF: LightOnOff_sw1.2, RA46.1, RA47.1; also elsewhere on the board
i_neutral: RearDevs1.7; also elsewhere on the board
i_powerOFF: D3.1 (K), powerOFF1.2; also elsewhere on the board
i_rightArrow: leftCtrls_conn1.5; also elsewhere on the board
i_startButton: rightCtrls_conn1.4; also elsewhere on the board
i_upLight: leftCtrls_conn1.4; also elsewhere on the board
o_engineON: RA2.1; also elsewhere on the board
o_keepAlive: R11.2, R12.2; also elsewhere on the board
tempPower: C2.1, K1.A1, Q3.5 (D_1), Q3.6 (D_2), Q3.7 (D_3), Q3.8 (D_4), Q3.9 (D_5), U2.1 (IN), koso-1.2, rearDevsPwr1.2; also elsewhere on the board

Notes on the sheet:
1) Start butt. (orange) 2) GND (blue) 3) Brake sw. (light blue) 4) Start butt. (black/white) 5) Engine OFF (black) 6) Engine ON (yellow/black)
1) GND (gray) 2) Left arrow (light blue) 3) DOWN light (white) 4) UP Light (blue) 5) Right Arrow (orange) 6) Horn (verde) 7) Clutch switch 8) N.C.
1) Rear light 2) Left arrow light 3) Right arrow light 4) Byke stand switch 5) Rear brake switch 6) START relay 7) Neutral gear switch 8) Eng-off CDI
CDI

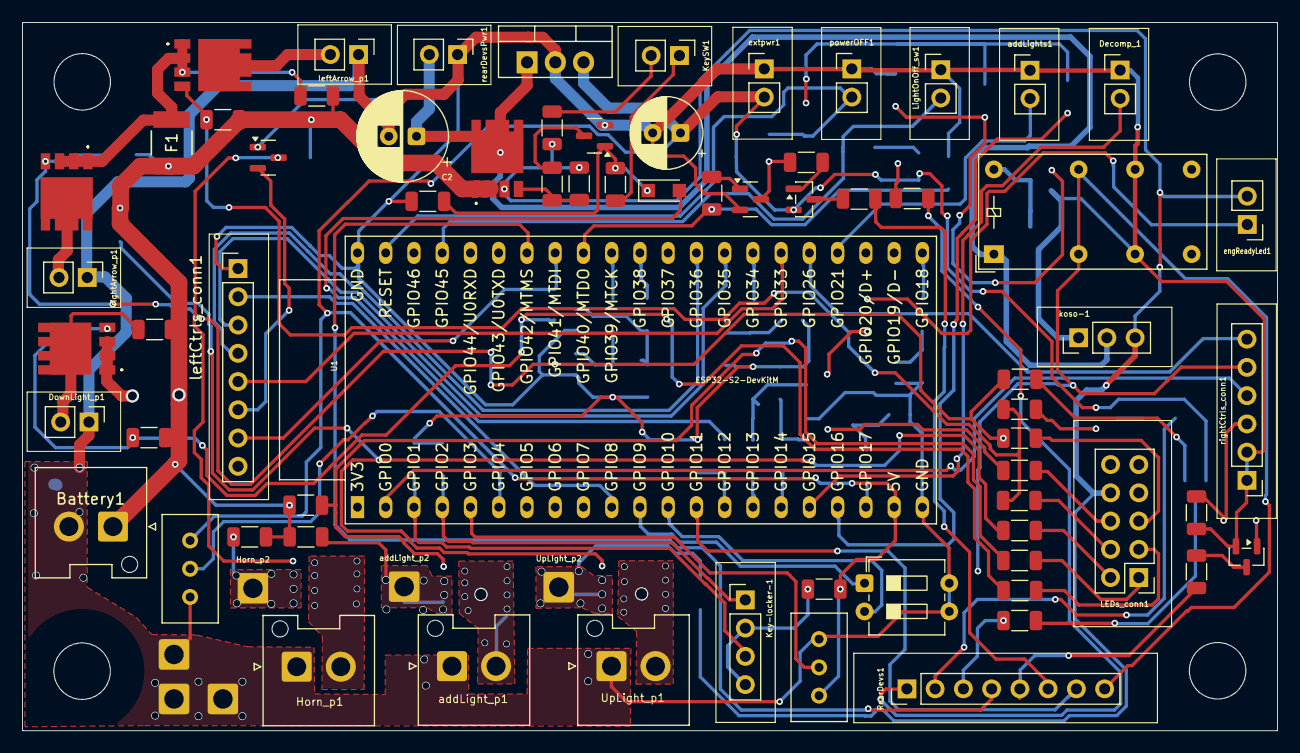
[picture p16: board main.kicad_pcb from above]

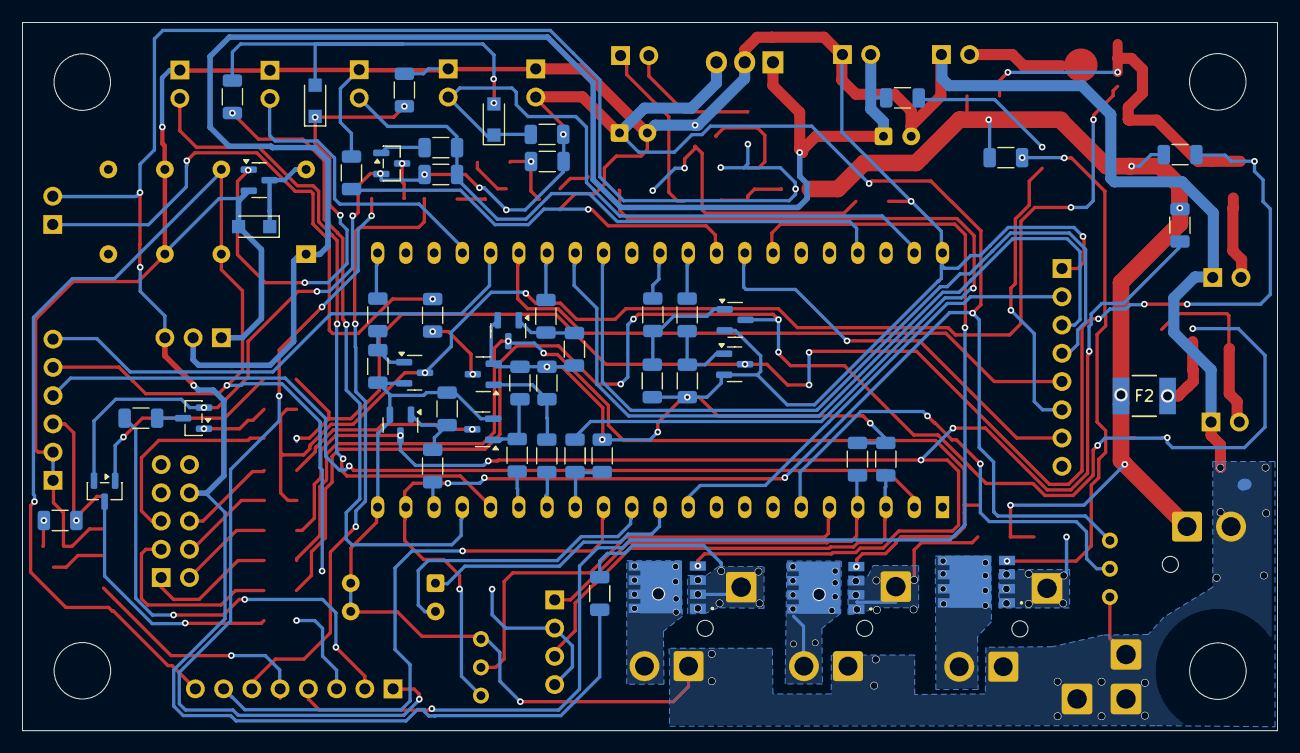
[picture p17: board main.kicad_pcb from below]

Board: 2 copper layers, 112.9 x 63.7 mm, 125 parts (51 on the bottom side), 97 nets.

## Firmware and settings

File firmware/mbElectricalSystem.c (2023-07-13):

/*------------------------------------------------------------------------------------------------------------------------------
//
//  __  __       _             _     _ _          _____ _           _        _           _   ____            _                 
// |  \/  | ___ | |_ ___  _ __| |__ (_) | _____  | ____| | ___  ___| |_ _ __(_) ___ __ _| | / ___| _   _ ___| |_ ___ _ __ ___  
// | |\/| |/ _ \| __/ _ \| '__| '_ \| | |/ / _ \ |  _| | |/ _ \/ __| __| '__| |/ __/ _` | | \___ \| | | / __| __/ _ \ '_ ` _ \
// | |  | | (_) | || (_) | |  | |_) | |   <  __/ | |___| |  __/ (__| |_| |  | | (_| (_| | |  ___) | |_| \__ \ ||  __/ | | | | |
// |_|  |_|\___/ \__\___/|_|  |_.__/|_|_|\_\___| |_____|_|\___|\___|\__|_|  |_|\___\__,_|_| |____/ \__, |___/\__\___|_| |_| |_|
//                                                                                                 |___/                       
//
// File:   mbElectricalSystem.c
//
// Author: Silvano Catinella <catinella@yahoo.com>
//
// Description:
//	This file contains all software needed by the ATmega16 to manage your motorbike's services (eg. start, stop, lights...)
//	In order to build the binary file I used XC-8 compiler, you can download it by the Microchip's website
//
//	Settings:
//		BLINK_DELAY     4000000
//		V_TOLERANCE     2       // 1 = 19mV
//		BUTTON_DEBOUNC  10000
//
// License:
//	Copyright (C) 2023 Silvano Catinella <catinella@yahoo.com>
//
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
------------------------------------------------------------------------------------------------------------------------------*/

#include <avr/io.h>
#include <stdlib.h>
#include <stdint.h>
#include <stdbool.h>
#include <mbesUtilities.h>
#include <mbesSerialConsole.h>
#include <mbesSelector.h>
#include <mbesPinsMap.h>


#define BLINK_DELAY     4000000
#define V_TOLERANCE     10
#define BUTTON_DEBOUNC  10000
#define ACHANS_NUMBER   4

//------------------------------------------------------------------------------------------------------------------------------
//                                                 F U N C T I O N S
//------------------------------------------------------------------------------------------------------------------------------

uint16_t ADC_read (const char *code) {
	//
	// Description:
	//	It _selects the argument defined channel and converts the voltage analog-value on that channel
	//
	//	ADMUX register:
	//		+-------+-------+-------+------+------+------+------+------+
	//		| REFS1 | REFS0 | ADLAR | MUX4 | MUX3 | MUX2 | MUX1 | MUX0 |
	//		+-------+-------+-------+------+------+------+------+------+
	//		|   0   |   0   |   1   |   0  |   0  |   0  |   0  |   0  |  Reset
	//		+-------+-------+-------+------+------+------+------+------+
	//		REFS1==0 & REFS0==0 ---> external volt ref
	//		ADLAR==1            ---> left giustified result
	//
	uint8_t pinNumber;
	codeConverter(code, NULL, &pinNumber);

	if (pinNumber < ACHANS_NUMBER) {
		ADMUX &= 0x20;                 // ADMUX register initialization
		ADMUX |= pinNumber;              // Analog channel _selection
	
		ADCSRA |= (1 << ADSC);         // Convertion starting...

		while (ADCSRA & (1 << ADSC));  // Waiting for convertion operation
	}

	return ADC;
}


uint8_t blink() {
	//
	// Description:
	//	It returns 1 or 0 alternating after a given time
	//
	static uint8_t  status = 0;
	static uint32_t counter = 0;

	if (counter >= BLINK_DELAY) {
		if (status == 0) status = 1;
		else             status = 0;
		counter = 0;
	} else
		counter++;

	return(status);
}


void setPinValue (const char *code, uint8_t value) {
	//
	// Description:
	//	It set the argument defined boolean value to the output pin
	//
	char    port;
	uint8_t pinNumber;

	codeConverter(code, &port, &pinNumber);

	if      (port == 'A' && value) PORTA |=  (1 << pinNumber);
	if      (port == 'A')          PORTA &= ~(1 << pinNumber);
	else if (port == 'B' && value) PORTB |=  (1 << pinNumber);
	else if (port == 'B')          PORTB &= ~(1 << pinNumber);
	else if (port == 'C' && value) PORTC |=  (1 << pinNumber);
	else if (port == 'C')          PORTC &= ~(1 << pinNumber);
	else if (port == 'D' && value) PORTD |=  (1 << pinNumber);
	else if (port == 'D')          PORTD &= ~(1 << pinNumber);
	else {
		// ERROR!
	}

	return;
}

//------------------------------------------------------------------------------------------------------------------------------
//                                                      M A I N
//------------------------------------------------------------------------------------------------------------------------------

int main(void) {
	uint8_t  loop             = 1; // It enables the main loop (Just for future applications)
	uint8_t  ready_flag       = 0; // When the flag is true (1), the motorbike is ready to accept commands
	uint8_t  FSM              = 0;
	
	struct mbesSelector 
		leftArr_sel, rightArr_sel, dLight_sel, uLight_sel, horn_sel, engStart_sel, decomp_sel, addLight_sel, light_sel,
		 engOn_sel
	;
	
	//
	// PINs direction setting
	//
	pinDirectionRegister(i_NEUTRAL,     INPUT);
	pinDirectionRegister(i_BIKESTAND,   INPUT);
	pinDirectionRegister(o_ENGINEOFF,   OUTPUT);
	pinDirectionRegister(o_ENGINEREADY, OUTPUT);
	pinDirectionRegister(o_NEUTRAL,     OUTPUT);
	pinDirectionRegister(o_RIGHTARROW,  OUTPUT);
	pinDirectionRegister(o_LEFTARROW,   OUTPUT);
	pinDirectionRegister(o_DOWNLIGHT,   OUTPUT);
	pinDirectionRegister(o_UPLIGHT,     OUTPUT);
	pinDirectionRegister(o_ADDLIGHT,    OUTPUT);
	pinDirectionRegister(o_HORN,        OUTPUT);
	pinDirectionRegister(o_KEEPALIVE,   OUTPUT);
	pinDirectionRegister(o_STARTENGINE, OUTPUT);
	
	
	//
	// _selectors initialization
	//
	mbesSelector_init(&horn_sel,     BUTTON, i_HORN);
	mbesSelector_init(&engStart_sel, BUTTON, i_STARTBUTTON);
	mbesSelector_init(&decomp_sel,   BUTTON, i_DECOMPRESS);
	mbesSelector_init(&leftArr_sel,  SWITCH, i_LEFTARROW);
	mbesSelector_init(&dLight_sel,   SWITCH, i_DOWNLIGHT);
	mbesSelector_init(&uLight_sel,   SWITCH, i_UPLIGHT);
	mbesSelector_init(&rightArr_sel, SWITCH, i_RIGHTARROW);
	mbesSelector_init(&addLight_sel, SWITCH, i_ADDLIGHT);
	mbesSelector_init(&light_sel,    SWITCH, i_LIGHTONOFF);
	mbesSelector_init(&engOn_sel,    SWITCH, i_ENGINEON);

	

	//
	// A/D converter settings....
	//
	ADCSRA = (1 << ADEN);    // A/D converter enabling
	

	//
	// Starting conditions
	//
	setPinValue(o_RIGHTARROW,  0);
	setPinValue(o_LEFTARROW,   0);
	setPinValue(o_DOWNLIGHT,   0);
	setPinValue(o_UPLIGHT,     0);
	setPinValue(o_ADDLIGHT,    0);
	setPinValue(o_HORN,        0);
	setPinValue(o_KEEPALIVE,   0); // IMPORTANT!!
	setPinValue(o_STARTENGINE, 0);
	setPinValue(o_ENGINEOFF,   1);


	// USART port initialization
	USART_Init(9600);


	while (loop) {
		if (ready_flag == 0) {
			//
			// Resistor keys evaluation
			//
			if (
				abs(ADC_read(i_VX1) - ADC_read(i_VY1)) < V_TOLERANCE &&
				abs(ADC_read(i_VX2) - ADC_read(i_VY2)) < V_TOLERANCE 
			) {
				// The keyword has been authenicated, you can unplug it
				setPinValue(o_KEEPALIVE, 1);
				ready_flag = 1;

			} else {
				// Waiting (1ms) to prevent brutal-force attack and for analog circuit re-initialization
			}
		
		} else {
			//
			// Lights and horn
			//
			if (mbesSelector_get(light_sel)) {
				setPinValue(o_DOWNLIGHT, mbesSelector_get(dLight_sel));
				setPinValue(o_UPLIGHT,   mbesSelector_get(uLight_sel));
			}
			setPinValue(o_HORN,     mbesSelector_get(horn_sel));
			setPinValue(o_ADDLIGHT, mbesSelector_get(addLight_sel));
			setPinValue(o_NEUTRAL,  !(getPinValue(i_NEUTRAL)));


			//
			// Blinking lights
			//
			if (mbesSelector_get(leftArr_sel)) {
				setPinValue(o_LEFTARROW,  blink());
				setPinValue(o_RIGHTARROW, 0);

			} else if (mbesSelector_get(rightArr_sel)) {
				setPinValue(o_RIGHTARROW, blink());
				setPinValue(o_LEFTARROW,  0);

			} else {
				setPinValue(o_RIGHTARROW, 0);
				setPinValue(o_LEFTARROW,  0);
			}
			
				
			// Decompressor sensor management
			if (FSM == 1) {
				if (mbesSelector_get(engOn_sel)) { 
					setPinValue(o_ENGINEOFF, 0);
					if (mbesSelector_get(decomp_sel)) FSM = 2;
				} else
					setPinValue(o_ENGINEOFF, 1); // 1 means eng locked

				
			// Electric starter engine starting...
			} else if (FSM == 2) {
				if (mbesSelector_get(engOn_sel) == false) 
					FSM = 1;
					
				else if (getPinValue(i_NEUTRAL) == 0) {
					 // The electric starter motor is rounding!!
					 if (mbesSelector_get(engStart_sel)) {
						setPinValue(o_STARTENGINE, 1);
						FSM = 3;
					}
				} else
					// Electric starter engine off
					setPinValue(o_STARTENGINE, 1);


			// Electric starter engine stopping...
			} else if (FSM == 3) {
				// EngOn == false
				if (mbesSelector_get(engOn_sel) == false || mbesSelector_get(engStart_sel) == false) {
					FSM = 1;
					setPinValue(o_STARTENGINE, 0);
				}	
			}
		}
	}

	return(0);
}

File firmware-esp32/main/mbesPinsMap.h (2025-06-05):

/*------------------------------------------------------------------------------------------------------------------------------
//
//  __  __       _             _     _ _          _____ _           _        _           _   ____            _                 
// |  \/  | ___ | |_ ___  _ __| |__ (_) | _____  | ____| | ___  ___| |_ _ __(_) ___ __ _| | / ___| _   _ ___| |_ ___ _ __ ___  
// | |\/| |/ _ \| __/ _ \| '__| '_ \| | |/ / _ \ |  _| | |/ _ \/ __| __| '__| |/ __/ _` | | \___ \| | | / __| __/ _ \ '_ ` _ \
// | |  | | (_) | || (_) | |  | |_) | |   <  __/ | |___| |  __/ (__| |_| |  | | (_| (_| | |  ___) | |_| \__ \ ||  __/ | | | | |
// |_|  |_|\___/ \__\___/|_|  |_.__/|_|_|\_\___| |_____|_|\___|\___|\__|_|  |_|\___\__,_|_| |____/ \__, |___/\__\___|_| |_| |_|
//                                                                                                 |___/                       
//
// File:   mbesPinsMap.h
//
// Author: Silvano Catinella <catinella@yahoo.com>
//
//
//	Symbol description:
//		+---------------+------------------+-----------------------------------------------------+
//		|     Symbol    |    Plug/link     |      Description                                    |
//		+---------------+------------------+-----------------------------------------------------+
//		| i_VX1         | resistors-key    | first voltage value                                 |
//		| i_VX2         |                  | second  "       "                                   |
//		+---------------+------------------+-----------------------------------------------------+
//		| i_VREF1       |  internal link   | first voltage reference                             |
//		| i_VREF2       |                  | second  "         "                                 |
//		+---------------+------------------+-----------------------------------------------------+
//		| i_NEUTRAL     | from gearbox     | it is 0 when the gear is in neutral position        |
//		+---------------+------------------+-----------------------------------------------------+
//		| i_DECOMPRESS  | from decompress. | it is 0 when decompressor has been pushes           |
//		+---------------+------------------+-----------------------------------------------------+
//		| o_KEEPALIVE   | internal only    | it keeps the system on when you unplug the key      |
//		+---------------+------------------+-----------------------------------------------------+
//		| i_BIKESTAND   | from bikestand   | it is 0 when the bike is placed on the stand        |
//		+---------------+------------------+-----------------------------------------------------+
//		| i_ADDLIGHT    | from ext. switch | additional high power light                         |
//		+---------------+------------------+-----------------------------------------------------+
//		| i_LIGHTONOFF  | from ext. switch | it turns on the normal lights (low/dazzling beam)   |
//		+---------------+------------------+-----------------------------------------------------+
//		| o_STARTENGINE | rear mtb. side   | it activates the (NO) engine-relay                  |
//		+---------------+------------------+-----------------------------------------------------+
//		| i_LEFTARROW   |                  | left turn blinking indicator switch                 |
//		| i_RIGHTARROW  |                  | right turn blinking indicator switch                |
//		| i_DOWNLIGHT   | left controls    |                                                     |
//		| i_UPLIGHT     |                  | dazzling beam command                               |
//		| i_HORN        |                  | horn button                                         |
//		| i_CLUTCH      |                  | 0 means the engine is NOT connected to the wheels   |
//		+---------------+------------------+-----------------------------------------------------+
//		| i_STARTBUTTON |                  | the tipical motorbike engine start button           |
//		| i_BRAKESWITCH | right controls   | the switch on the front brake command               |
//		| i_ENGINEON    |                  | the on/off engine switch in on-position             |
//		+---------------+------------------+-----------------------------------------------------+
//		| o_ENGINEREADY |                  |                                                     |
//		| o_NEUTRAL     |                  |                                                     |
//		| o_RIGHTARROW  |   cockpit LED    |                                                     |
//		| o_LEFTARROW   | indicators and   |                                                     |
//		| o_DOWNLIGHT   |    services      |                                                     |
//		| o_UPLIGHT     |                  |                                                     |
//		| o_ADDLIGHT    |                  |                                                     |
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

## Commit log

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2023-05-31 Fix: wrong power transistor orientation (and PCB's size reducing)
    [motorbike_electrical_system.kicad_pcb]
2023-06-03 enhancement: BDX34C replaced by D45VH10
    In order to reduce the wasted electric power BDX34C (VCE=2.5V) has been replaced by D45VH10 (VCE=0.3V) for up-light and added-light
    [motorbike_electrical_system.kicad_pcb, motorbike_electrical_system.kicad_sch]
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2023-06-16 fix: duplicated signal
    [motorbike_electrical_system.kicad_pcb, motorbike_electrical_system.kicad_sch]
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2023-06-16 fix: missing Vy(1,2) references for the key authentication
    [motorbike_electrical_system.kicad_pcb, motorbike_electrical_system.kicad_sch]
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2023-06-18 feat: power-off button
    Because MCU could have a problem for an unpredictable reason, a power-off button has been added to stop the current to the MCU.
    But, because I am paranoide and the transistor could have problems, I connected the power-off button yo the MCU too. In this way
    it can always shutdown itself
    [mbes_front_outputs.kicad_sch, mbes_inputs.kicad_sch, motorbike_electrical_system.kicad_pcb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]
2023-06-19 Floating BC337 transistors bases fixed, and PowerOFF button management added
    [mbes_front_outputs.kicad_sch, motorbike_electrical_system.kicad_pcb, motorbike_electrical_system.kicad_sch]
2023-06-19 - Other floating BC337 transistors bases fixed - USB port missing fixed - Small enhancements
    [mbes_front_outputs.kicad_sch, mbes_inputs.kicad_sch, motorbike_electrical_system.kicad_pcb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]
2023-06-21 Fix: porting to AVR code
    For a (ChatGPT) mistake the last versions was implemented for the PIC architecture. I have ported the code to AVR architecture
    (xc.h --> avr/io.h)
    [mbElectricalSystem.c]
2023-06-21 Fix: porting to AVR code
    [mbElectricalSystem.c]
2023-06-21 External cockpit power-connector added and wrong transistor type fixed
    [mbes_front_outputs.kicad_sch, mbes_inputs.kicad_sch, motorbike_electrical_system.kicad_pcb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]
2023-06-22 Fixes and optimizations (unuseful I/O lines dropped)
    [mbes_front_outputs.kicad_sch, mbes_inputs.kicad_sch, mbes_rear_connector.kicad_sch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]
2023-06-23 Fixes and updates due to the PCB changes
    [mbElectricalSystem.c]
2023-06-23 Many fixes. This release get no error by XC8 in binary building
    [mbElectricalSystem.c]
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2023-07-08 AVR Timers simulation fixed
    The POSIX timers (create_timer()) provide only the countdown mode, so I have simulated the AVR's ones using the timeofday()
    function and a t0 refence. At the moment a small problem on hold-buttons is surviving.
2023-07-09 fix for mbesSelector_update(): FSM fixed for hold-buttons management
2023-07-10 Fixes and small refactoring
    [mbElectricalSystem.c]
2023-07-11 This Makefile has been written for XC8 compiler
    Unfortunately it returns strange error on not-valid chartacters used inside the source code. For this reason, I switched to
    AVR-GCC. This compiler does not return me that error.
2023-07-17 PCB splitted
    In order to use the debug support, it has been needed to add the ISP port. But it means to loose 4 pins.
    So, I have added a I/O extender chip on I2C bus (other 2 pins lost). Because the complexity has encreased
    I have had to split the PCB in thwo different ones.
    [conn_to_pcbb.kicad_sch, mbes_inputs.kicad_sch, mbes_rear_connector.kicad_sch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]
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2023-07-24 Wrong relay's footprint fixed
    [mbes_start_stop.kicad_sch, pcb-b.kicad_pcb, pcb-b.kicad_sch]
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2023-07-24 small fix
    [pcb-a.kicad_sch]
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2023-07-26 Refactoring: only not critical I/O on MCP23008XP
    I know also MCP23008XP is under military standards, but I want my motorbike still be usable after the MCP23008XP is broken
    [pcb-a.kicad_pcb, pcb-a.kicad_sch]
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2023-07-26 small errors and warnings fixed. Ready to be printed
    [pcb-a.kicad_pcb, pcb-b.kicad_pcb]
2023-07-27 Unusefull components removing and RS232 connected also to PCB-b
    - The low-pass filter on RS232 RXD has been removed because external serial cable idea has been dropped
    - The RS232 lines are been connected also to the PCB-b for future (CH5 module) Bluetooth implementation
    [conn_to_pcbb.kicad_sch, pcb-a.kicad_pcb, pcb-a.kicad_sch]
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2023-08-09 Fix for (USB-ASP compliant) ISP-10pin connector
    [pcb-a.kicad_pcb, pcb-a.kicad_sch]
2023-08-20 Wrong position for VTAG pin fixed
    [pcb-a.kicad_pcb, pcb-a.kicad_sch]
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2023-09-10 Fix: RESET pin and RS232 port fingerprint
    - pull-up resistor added to RESET pin
    - RS232 port fingerprint resized to standard 4-pin port
    [pcb-a.kicad_pcb, pcb-a.kicad_sch]
2023-09-30 External oscillator
    [pcb-a.kicad_pcb, pcb-a.kicad_sch]
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2023-10-01 Fix for USART_Init()
    Using the U2X bit the prescaler allows you to use higher BPS in UART communication.
    With external 8Mhz oscillator and U2X = 0, data tranfer fails over the 2400bps. But, with U2X =1 I have successfully tested 9600bps
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2023-10-01 Fixes for fuses-update rule
2023-10-01 Wrong capacitors type fixed
    [pcb-a.kicad_pcb, pcb-a.kicad_sch]
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2023-10-21 Enhancement: RS232 port
    RS232 4-wire connector is compatible with MAX232 driver module
    [pcb-a.kicad_pcb, pcb-a.kicad_sch]
2023-10-28 Fixes for analog inputs
    - ground reference missed
    - AVCC was not connected
    [pcb-a.kicad_pcb, pcb-a.kicad_sch]
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2023-11-04 Wrong I2C_CLOCK_FREQ value fixed.
    Now, it should be ok for 10Khz I2C bus frequency
2023-11-05 Pull-up resistors missing on I2C has been fixed
    [pcb-a.kicad_pcb, pcb-a.kicad_sch]
2023-11-06 Fixes
    - Device address is now stored inside the module, statically
    - No device address inside function's arguments list
    - Fixes
2023-11-09 Fix for init_MC2398()
    I2C bus initialization missed
2023-11-09 Fix for I2C_init(): I2C enabling bit
2023-11-12 New experimental implementation
    The last (firmware4) test shown a new problem: RAM full error at compile time. For this reason, I converted some I2C library's
    function to macro. But it has made the code-size bigger :-(
    I am valuating the possibility to switch to AT-Mega32 MCU
2023-11-15 New speed default setting
    The new default speed for the ASCII serial console is 9600 bps. It is the maximum speed you can use with the standard
    fuses configuration, it means you are using 1Mhz internal oscillator.
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2023-12-15 Wrong register check fixed and performance enhancement
    - The check for GPIO has been removed (while I press/release the button the reg changes!)
    - Becase the seq. reaging has been disable (in IOCON setting), use I2C stop is not required on GPIO-loop.
    - Console messages have been removed in no-debug mode
    This version has been successfully tested!
2024-01-05 mbesSelector has been temporary disabled
    Due to mbesUtilities library changes, I have to adjust this library to manage also the I2C-BUS error events.
    But before this huge step, I want to get all (firmware<n>-test) tests to cover the used libraries
2024-01-05 Fixes for the pins management functions
    - The source code has been rewritten using the mbesMCP23008 component.
    - The APIs has been changed to manage the I2C errors
2024-01-06 Wrong pin-names fixed
2024-01-06 Small fix for I2C_READ() macro
    - status messages were out of debug-messages policy rule
2024-01-06 debug messages fixed and new ones added
    In this release, the initialization has been succesfully tested. But in the MCP23008's pin
    management there is still a problem. When the main loop starts to read GPIO register, the
    retrived value is 215!!! But the expected value is 255
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2024-01-11 Functions prototypes fixed
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2024-01-21 Changes and porting to KiCAD-7.0
    The MCP23008's reset PIN is no more connected to the MCU's reset. Now, it is connected to the A4 MCU's pin.
    This change allows the MCU to reset the I2C connected device, when there are too many errors
    [pcb-a.kicad_pcb, pcb-a.kicad_sch]
2024-01-30 Automatic fabric-data creation
    This script allows you to create the zip-file with all files needed by a PCB maker to create the script's argument defined PCB
    WARNING! At the moment kicad-cli returns an error, it could be a Kicad's bug, probably
2024-02-10 o_MCPDEVRESET pin definition added
    This pin allows the MCU to reset the MCP23008 device
    [mbesPinsMap.h]
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2024-02-10 reset_MCP23008() prototype added
2024-02-13 Fix for I2C_STOP() macro
    This is not-tested change and it should be not needed, but it can be a good enhancement. In fact, with this fix the I2C stop-signal
    should become a blocked instruction. It means that it will allow me to reduce the forced delay steps.
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2024-02-18 Unrecognized char trouble fixed
    The integration tests have shown a problem on the first received char. This invisible one, make (often but not
    always) fail the pin definitioon syntax matching. I was unable to discover this character, in Perl, (Perl is not C), so
    I modified the regex to be a more generic one. It is just a workaround. But, at the moment, it functions very well
2024-02-19 Fix for I2C_STOP() macro
    As Bard wrote me, AVR micro provides TWSTO bit for write-once operation. Reading this bit returns not predictable value
2024-03-02 Fixes for mbesSelector_update()
    The debouncing time support has been removed when the selector type mis SWITCH
2024-03-03 Fixes for the motorbike start procedure
2024-03-14 i_DOWNLIGHT removed
    The traditional old type left control has a selector to control the down/up light. In fact, starting to develop the code
    using this device type, I defined i_DOWNLIGHT input pin to control the down-light status. But, because I broke the device
    I searched for a better solution, and I find a new device type where the switch has been replaced with a button for the
    up-light only. Because I don't manage the day-light, this solution bring me just advantages: I can save a pin, and I can
    provide a better using for the light-on/off using
    [mbesPinsMap.h]
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2024-04-01 Changes fot WAIT4TWINT() macro and I2C_CLOCK_FREQ fixed
    - The I2c clock has been increased to 200Khz
    - The step-by-step delay has been decreese under one millisecond
2024-04-06 MAX232CPE added
    In order to see the log messages when the device is mounted on motobike, I need to put the RS232 plug into the device directly.
    For this reason I added the RS232 transciver to the circuit
    [pcb-a.kicad_sch]
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2024-04-14 Rollback
    It will be the last version using DIP. I have to accept it is an old technology, this PCB would be a great result in the 2000 age
    but a century quarter is past! :-( It is the SMD age, now. So, after the second upograde of my laboratory, I will rebuild the
    PCB using SMDs.
    [mbes_inputs.kicad_sch, pcb-a.kicad_sch]
2024-04-26 Wrong power management fixed
    - Some internal AT-Mega-16's parts were powered by 5V line, directly. They are correctly connected to temp-power, now.
    - Small fix dor the MAX232 chip
    [pcb-a.kicad_pcb, pcb-a.kicad_sch]
2024-04-27 Fix and changes for self-power-suppling system
    Because the PCB-B should be responsible just for power switching management and PCB-A for the control logic, the
    self-power-suppling system has been moved from pcb-b to pcb-a. It should be easier to debug too
    [conn_to_pcbb.kicad_sch, mbes_inputs.kicad_sch, mbes_start_stop.kicad_sch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]
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2024-05-16 Many changes
    - The power drivers component has been implemented with TPCA8120 P-ch MOSfet
    - The temp-power management has been moved from pcb-a to pcb-b
    [conn_to_pcbb.kicad_sch, mbes_front_outputs.kicad_sch, mbes_inputs.kicad_sch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]
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2024-06-16 SSR replace mechanical retlay
    Not yet been tested
    [mbes_start_stop.kicad_sch]
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2024-06-20 Change for Key PCB's connector
    The two pin on tempPower are now connected to the PCB-B, because all the temp-power management have been provided by the PCB-B
    So the connector on PCB-A is a 4 pins one
    [mbes_inputs.kicad_sch]
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2024-06-21 PCB-A size reducing
    Now PCB-B and PCB-A fits almost perfectly, but not the pin-header connectors. I will use wires instead. But they can be mnounted A on top of B ;-)
    [conn_to_pcbb.kicad_sch, mbes_inputs.kicad_sch, pcb-a.kicad_pcb]
2024-06-30 Changes and enhancements
    - File porting to Kicad-8
    - Size reducing
    - SSR has been replaced by Mosfet deplation N-Channel
    [pcb-a.kicad_pcb, pcb-b.kicad_pcb]
2024-06-30 Changes and enhancements
    - "to-PCB-a-1" connector has been changed with tree pins one
    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
    [mbes_front_outputs.kicad_sch, mbes_start_stop.kicad_sch, pcb-b.kicad_sch]
2024-07-06 Size reducing and component rationalization
    - RS232(TTL) lines on PCB-B have been removed (MAX232 is already mounted in PCB-A)
    - The two PCB can no more be connected using pin-header connectors. You have to use welded wires, now.
    (this solution is not beautiful as the original, but it is a more flexible one and it also allowd me
    to reduce the PCB size)
    The PCBs size is approximately 109.7mm x 43.5mm.
    For this dual-face sigle-layer (THT) version this is the minimum size I can achieve.
    [conn_to_pcbb.kicad_sch, mbes_inputs.kicad_sch, mbes_rear_connector.kicad_sch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]
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2024-07-13 Line to border distance was too small
    [pcb-a.kicad_pcb]
2024-08-19 Wrong relay's power supply fixed
    [mbes_start_stop.kicad_sch, pcb-b.kicad_pcb]
2024-08-20 Pull-down resistor missing fixed
    [pcb-b.kicad_pcb, pcb-b.kicad_sch]
2024-08-22 More stable solution for BJT driving
    The BJT-817 device's sensibility is very high. If you are doing some test and you weld a wire to che i_PowerOFF pin, then you
    can find the transistor's sturation while the wire is not connected.
    [mbes_start_stop.kicad_sch, pcb-b.kicad_pcb]
2024-08-23 Unuseful wrong resistor deleted
    [pcb-b.kicad_pcb]
2024-08-26 USB Power Supply connector fixed
    [pcb-b.kicad_pcb, pcb-b.kicad_sch]
2024-08-28 ESP32 version
    Because I have had serious problems with my AVR programmer device ATMEL-ICE (Chineese version), and because a new original
    one (by Microchip) cost a lot of money, I have decided to change MCU, at the end we are living in the 2024!!! So, I am
    porting the solution to ESP32 MCU. In this preliminary version, I am using an ESP32-S2-DevKitM
    [mbes_inputs.kicad_sch, pcb-a.kicad_pcb, pcb-a.kicad_sch]
2024-09-05 Wrong PIN assignment fixed
    i_VX1 assigned to a no ADC service PIN
    [pcb-a.kicad_pcb, pcb-a.kicad_sch]
2024-09-05 Missing clutch sw added
    [mbes_inputs.kicad_sch, pcb-a.kicad_pcb, pcb-a.kicad_sch]
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2024-09-05 Unuseful wrong comments deleted
    [mbesPinsMap.h]
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2024-10-06 Wrong MCU ADC pins symbols fixed
    [mbesPinsMap.h]
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2024-10-07 Mutex has been added to avoid race condition
    [test05.c]
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2024-10-09 Wrong args in prototypes definitions
2024-10-09 Fixes and enhancements for _moduleDB_get()
    [iInputInterface.c]
2024-10-10 Fix for iInputInterface_new() and comments removed
    (many cut not all) comment used for debug have been removed
    This version has been fully tested, it function very well
    [iInputInterface.c]
2024-10-10 Many fixes and enhancements. 100% OK!
    [test06.c]
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2024-10-16 Small fix for iInputInterface_get()
    [iInputInterface.c]
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2024-10-17 Fix for _moduleDB_get()
    Shared memory has been marked as volatile resource
    [iInputInterface.c]
2024-10-17 Many fixes (100% building errors free)
    [prod.c]
2024-10-18 Updates for moduleDB using
    Refactoring to fix death-lock trouble
    [iInputInterface.c]
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2024-10-19 Many fixes
    - blinker() missing initialization fixed
    - app_main() nissing fixed
    - A/D converter wrong configuration fixes
    [prod.c]
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2024-10-22 Incorrect value in right-shift operaton fixed
    1 is different by 1ULL!!!!!!!!!!!
    [test02a.c]
2024-10-24 Refactoring
    In order to avoid pin insormation loosing, I changed API approach: no more function to send data directly to debug-console, now,
    the lib provides two wrapper to the input/output system api. Replacing these with the debug-console wrappers, you cannot loose
    pin status!!
    [debugConsoleAPI.c]
2024-10-24 Fix and updates due to debugConsoleAPI changes
    [prod.c]
2024-10-24 i_LEFTARROW pin has been moved to GPIO_NUM_8
    GPIO_NUM_46 can be defined as input-pin, only. But the biggest problem is that pull-up resistors have no effect. But if I connect
    3V power to the pin directly. it functions!!! This trouble would require a more exhaustive analisys
    [mbesPinsMap.h]
2024-10-24 i_LIGHTONOFF pin swapped with i_STARTBUTTON one
    The pin-0 (where is connected i_LIGHTONOFF) is used by the MCU to select which boot it has to perform. It means, if you turn-on
    your motorbike with the light turned-on, then the motorbike will be frozen. I have swapped with i_STARTBUTTON, because nobody
    turned-on his netal-horse with the start button already pushed!!!!
    [mbesPinsMap.h]
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2024-10-27 Old files replaced.
    They have been merged for error
    [mbes_front_outputs.kicad_sch, pcb-a.kicad_pcb, pcb-a.kicad_sch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]
2024-10-27 Fixes
    Files have been recovered from the situation before the last merge, and then fixed
    [mbes_front_outputs.kicad_sch, mbes_inputs.kicad_sch, mbes_pcbA_connectors.kicad_sch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]
2024-11-01 Enhancements
    - the four single-lines connectors to the MPU has been replaced by two dual-lines connectors. It is a great advantage in the
    PCB mounting, because the two-lines ones does not require to be welder!! The connectors are mounted using special pillers.
    - Because turn-indicator led-light use less then 100mA current, I have replaced the MOSFETS with BC327 NPN BJTs. In this way
    I have semoved the fuse. In fact the transistor is set to make flow just ((12/7K)*130) 223mA and it should not release more
    then 300mA in short-ciruit situation. So the fuse is not more needed.
    [mbes_front_outputs.kicad_sch, pcb-b.kicad_pcb, pcb-b.kicad_sch]
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2025-01-02 Update for connectors change
    The four connectors that linked pcb-a with pcb-b have been replaced with two dual line connectors.
    [mbes_pcbA_connectors.kicad_sch]
2025-01-04 Fixes and updates
    This version will be tested soon. It is fully implemented with THT devices using ESP32-S2 DevKit
    [mbes_pcbA_connectors.kicad_sch, pcb-a.kicad_pcb, pcb-a.kicad_sch]
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2025-01-06 Enhancement for direction-indicators circuit
    To make the circuit completely safe, I have added MSMF050-2 restatable-fuses to protect it vs short-circuits events.
    In order to prevent PNP transistors damages, I have also added a 3 Ohm 0.5W resistor composed by four 1206 SMD componets
    [mbes_front_outputs.kicad_sch, pcb-b.kicad_pcb]
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2025-03-01 Uncovered PCB support holes fixed
    [pcb-a.kicad_pcb]
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2025-03-31 Fixes and changes
    - 8pin pin-header connectors have been replaced with more standard 10pin connectors
    - Wrong components sizes have been fixed
    - too small solder-wire connectors have been fixed
    [mbes_front_outputs.kicad_sch, mbes_pcbA_connectors.kicad_sch, pcb-a.kicad_pcb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]
2025-05-21 hanges and fix
    - The R6 and R8 pull-up resistors have been removed. I will use internal ones
    - The J2 connector position has been moved
    [pcb-a.kicad_pcb, pcb-a.kicad_sch]
2025-05-29 Small syntax error fixed
    [mbesPinsMap.h]
2025-05-29 New version based on NCurses
    The main problem of this console has always been the screen flickering; because the display is rewritten every time the
    console read a new log, the displayed text is not stable and does not allow the user to read it in easyly way. For this
    reason I rewrote this software from Perl to C. The C version is absolutely better, but not yet enough.
    So, in order to achieve a better result, I have used NCurses library. The result is quiet better, but not enough, So, in
    the future I will convert the printing method from a sequential way to a positioonal one
2025-06-02 Fix and enhancement
    - i_BIKESTAND symbol fixed
    - NOAUTH symbol management added
    [prod.c]
2025-06-05 Small fixes...
    [mbes_pcbA_connectors.kicad_sch, pcb-a.kicad_pcb]
2025-06-05 Fix: wrong NOAUTH symbol switching
    [prod.c]
2025-06-06 Small size problem fixed
    [pcb-b.kicad_pcb]
2025-06-06 Fix: not common connector has been replaced
    The 8-pin flat-cable connector is not easy to find on market. It has been replaced with the 10-pin standard one
    [mbes_front_outputs.kicad_sch, pcb-b.kicad_pcb]
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2025-07-07 Fix stupid error on the direction indicators management
    [mbes_front_outputs.kicad_sch, pcb-b.kicad_pcb]
2025-07-11 Around connectors space problems fixed
    [pcb-b.kicad_pcb]
2025-07-29 Fix: o_KEEPALIVE wrong behavior in NOAUTH mode
    [prod.c]
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2025-08-03 Fix: parking mode after bootstrap
    In order to avoid unwanted parking mode selection, the commands sequence MUST keep selected for a time period.
    [prod.c]
2025-08-03 Fix: horn still usable also when the mb is off
    Horn is enabled by tempPower, now
    [mbes_front_outputs.kicad_sch, pcb-b.kicad_pcb]
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2025-08-05 Fix: cables exit hole
    In order to find an usable cables exit-hole I turned the box upside down. Now, the cover will be fixed on the motorbike
    framework and the bottom will take the koso cockpit.
    This version is not easy to weller, but it allows me to find enough space inside. In the cover locker the two cables exit
    holes have 8mm diameter instead of 16mm, it is required to avoid box deformation during the weller procedure. You have to
    modify the holes after.
    [DR350_rally.dxf]
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2025-08-07 Enhancement: the last BC337 has been replaced by a BC817
    [main.kicad_sch, mbes_front_outputs.kicad_sch]
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2025-08-08 Fixes and size reductuion
    - Mosfets' power lines have been added
    - 1.5 mm size reduction
    [main.kicad_pcb]
2026-02-26 Small fixes
    - Floating BC817's base fixed
    - EngReady_LED connector orientation fixed
    [mbes_front_outputs.kicad_sch, mbes_pcbA_connectors.kicad_sch]
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2026-02-26 Holes for cabeles have been fixed
    [DR350_rally.dxf]
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2026-03-03 new box lid locking system
    The old system was based on typical threaded clothespins used on motorbyke fearings. But these clothespins take up too much space.
    So, in order to save some precious millimeter I used sqare bars with threaded holes on the two faces. The bars attach the lid
    support to the walls of the box.
    [DR350_rally.dxf, DR350_rally_stainless_steel.dxf]
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2026-03-18 Wrong electric track size fixed
    [main.kicad_pcb]
2026-03-24 Many fixes and changes
    - Electric schema and PCB changes:
    - To avoid unwanted service starting (lights, electric start engine....), the signals from the motorbike's front side to
    the rear one, are no more connedted to the FET's gate directly. There is a second stage realized with PNPs transistors,
    now. It is a more stable and safe solution.
    - In the shcema:
    - All the c_<signal> symbols have been splitted in ci_<signal> and co_<signal>, and the symbols direction (input/output)
    have been fixed
    - To get a more readable schema, the c*_<signal> symbols have a different color
    [main.kicad_pcb, main.kicad_sch, mbes_front_outputs.kicad_sch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]
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2026-04-06 Merge from ESP32__dualPCB branch
    - DownLight: external fuse replaced by internal automatic one, wire connector replaced by 2.54 pin-header
    - The resistor between FET's gate and NPN's collector has been removed
    [main.kicad_pcb, main.kicad_sch, mbes_front_outputs.kicad_sch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]
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2026-04-06 JST connector orientation fixed (female for PCB)
    [main.kicad_pcb]
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2026-04-08 Fly-back diode's wrong value fixed (it is just a notation)
    [pcb-c.kicad_sch]
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2026-04-14 Merge from ESP32__dualPCB
    - Wrong diode footprints fixed
    - Floating FET's source pin fixed
    - Unuseful horn's propagation fixed
    [main.kicad_pcb, mbes_front_outputs.kicad_sch, mbes_pcbA_connectors.kicad_sch]
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
